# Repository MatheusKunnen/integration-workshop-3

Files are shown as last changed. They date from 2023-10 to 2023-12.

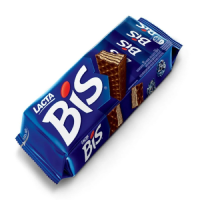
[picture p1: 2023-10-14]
server/images/bis.png

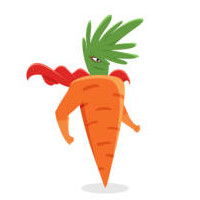
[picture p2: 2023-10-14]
server/images/p2i2.jpg

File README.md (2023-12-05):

# Snacks Control System

This project was created for the Integration Workshop 3 within the Computer Engineering curriculum during the second semester of 2023 at UTFPR University.

**Team Members**

- Alessandra Fernandes Lacerda
- Gabriel Henrique Linke
- Ivan Bauer Jr.
- Matheus Kunnen Ledesma _(Project Manager)_
- Meika Farias de Oliveira
- Patricia Abe Turato

**Orientators**

- Prof. Dr. Heitor Silvério Lopes
- Prof. Dr. João Alberto Fabro

## Overview

A frequent concern of parents is the difficulty in controlling their children's eating habits at school, as children need healthy snacks to support their growth and development. Unfortunately, many of the snacks provided in the school canteen are high in fat, sugar and salt. Furthermore, it is difficult to guarantee that children diagnosed with food allergies or intolerance do not eat foods containing ingredients that may cause a reaction. On top of that, kids might not know how to manage their money well and end up spending too much.

The project tries to solve these problems with a system that allows parents to manage the options of snacks shown to their kids, and a vending machine to distribute these snacks.

The mobile application allows parents to register their children in the system, select the specific snacks that will be available for them to buy and specify their daily budget. The vending machine identifies the child and shows all available authorized food options along with the available budget. Finally, when the desired product is selected, the machine asks for confirmation and then delivers the snack.

## Acknowledgements

The team would like to express their deepest gratitude to Professor Dr. Heitor Silvério Lopes and Professor Dr. João Alberto Fabro for their guidance and support during the development of the project. Also, the team is thankful to all the professors of Computer Engineering at UTFPR for their contributions to the team members academic growth. Their collective efforts in imparting knowledge and sharing experiences were fundamental to the development of capabilities that made this a successful project.

## Useful links

- Blog: https://alelacerda.notion.site/Snacks-Control-System-76155e9a51a641b1811bb6345904a688?pvs=4
- Video: https://youtu.be/sgXLWZ9KaMk

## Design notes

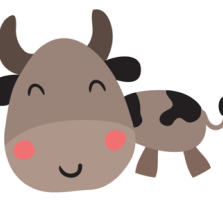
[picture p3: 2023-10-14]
server/images/p1i4.png

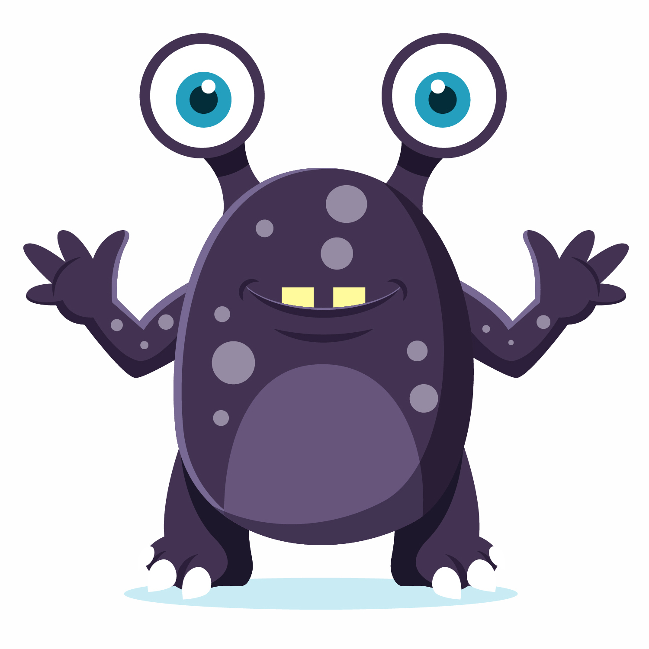
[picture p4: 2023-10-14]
server/images/p3i1.jpg

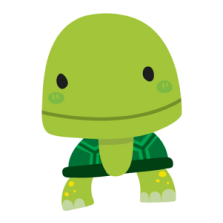
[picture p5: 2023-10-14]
server/images/p1i6.png

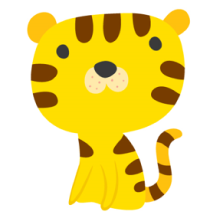
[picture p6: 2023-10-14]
server/images/p1i2.png

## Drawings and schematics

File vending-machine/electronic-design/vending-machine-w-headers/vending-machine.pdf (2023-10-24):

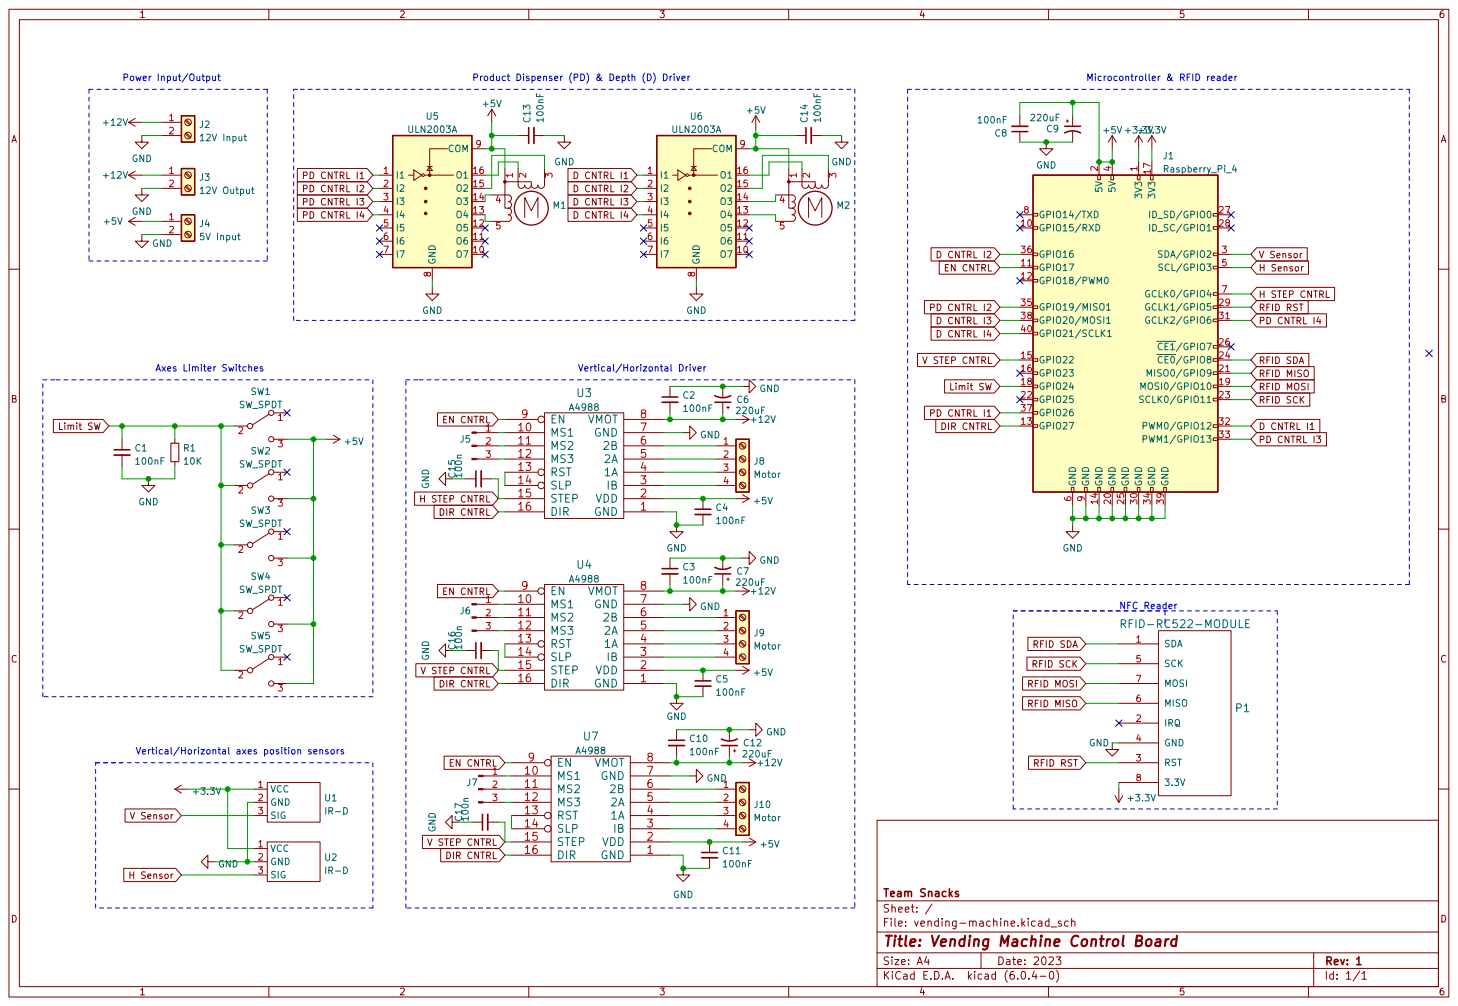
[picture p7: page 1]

8 COM 9 U6 ULN2003A GND GND GND

V Sensor H Sensor RFID RST PD CNTRL I4 PD CNTRL I3 H STEP CNTRL RFID SDA RFID MOSI RFID MISO

D CNTRL I1 RFID SCK RFID MOSI

EN CNTRL Limit SW

File: vending-machine.kicad_sch Sheet: / Team Snacks

Id: 1/1 Title: Vending Machine Control Board

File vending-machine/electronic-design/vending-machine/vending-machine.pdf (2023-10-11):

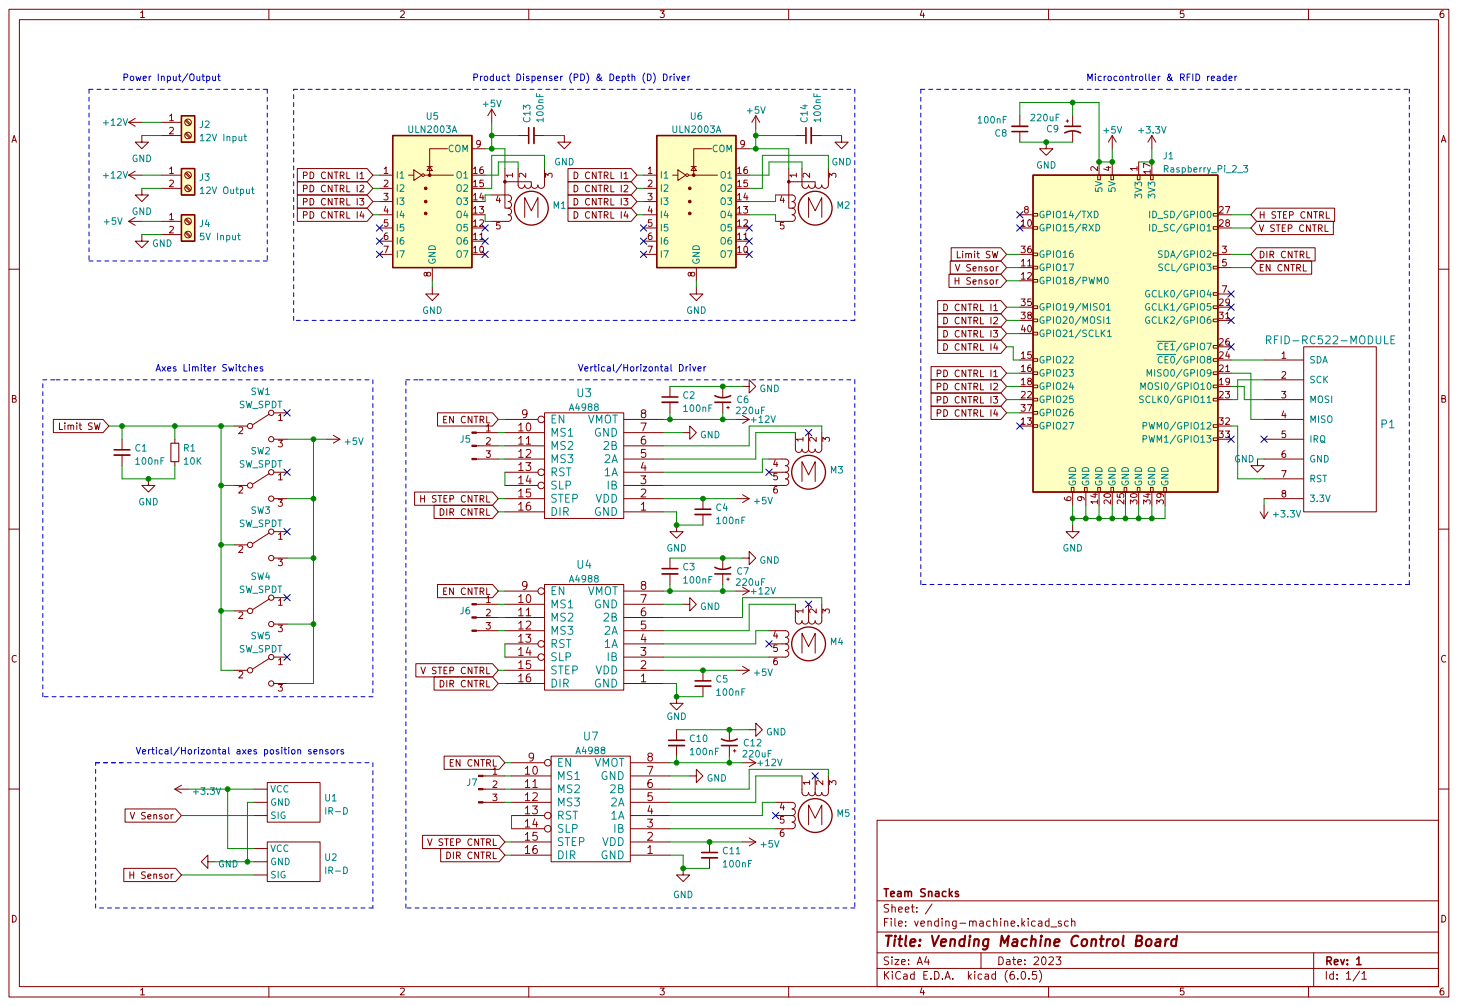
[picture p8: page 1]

H STEP CNTRL V STEP CNTRL EN CNTRL EN CNTRL

File: vending-machine.kicad_sch Sheet: / Team Snacks

Id: 1/1 Title: Vending Machine Control Board

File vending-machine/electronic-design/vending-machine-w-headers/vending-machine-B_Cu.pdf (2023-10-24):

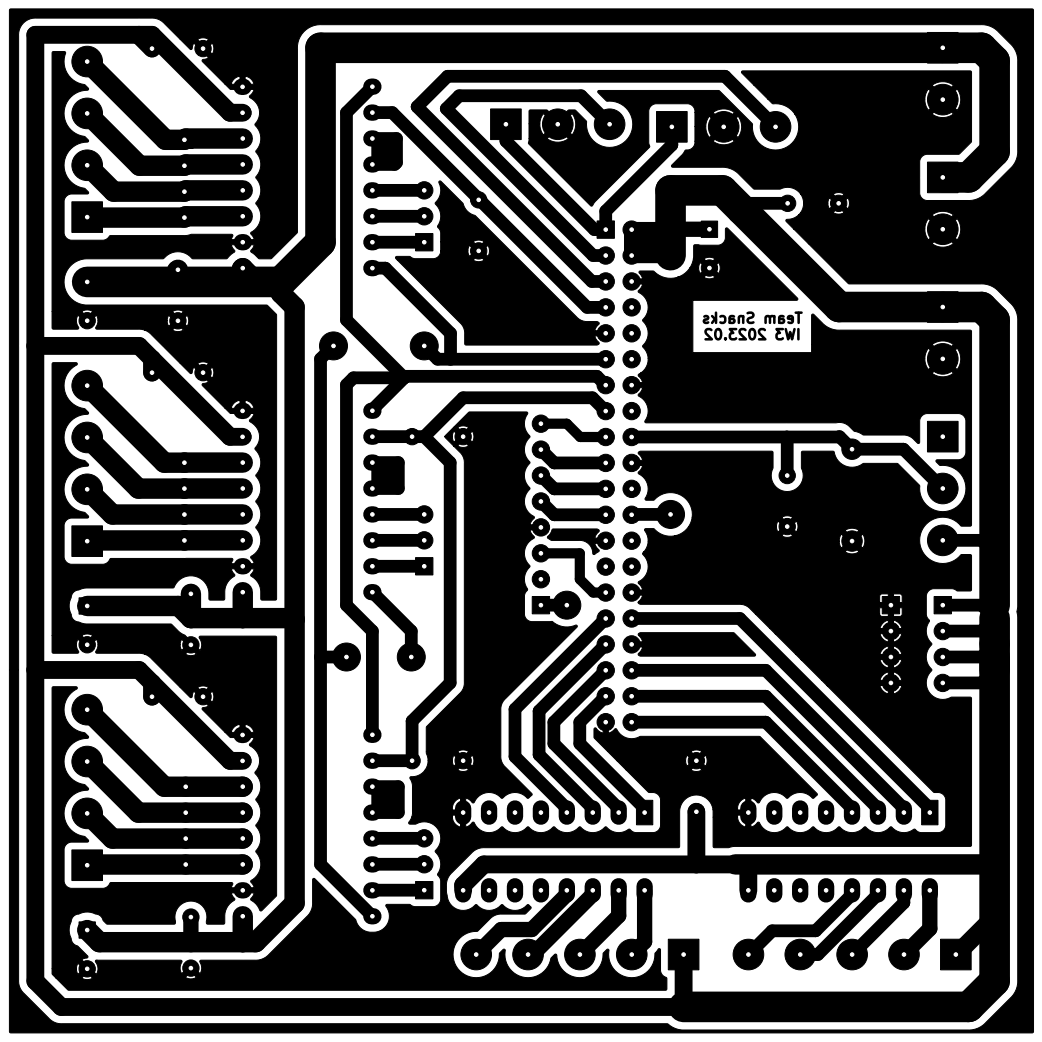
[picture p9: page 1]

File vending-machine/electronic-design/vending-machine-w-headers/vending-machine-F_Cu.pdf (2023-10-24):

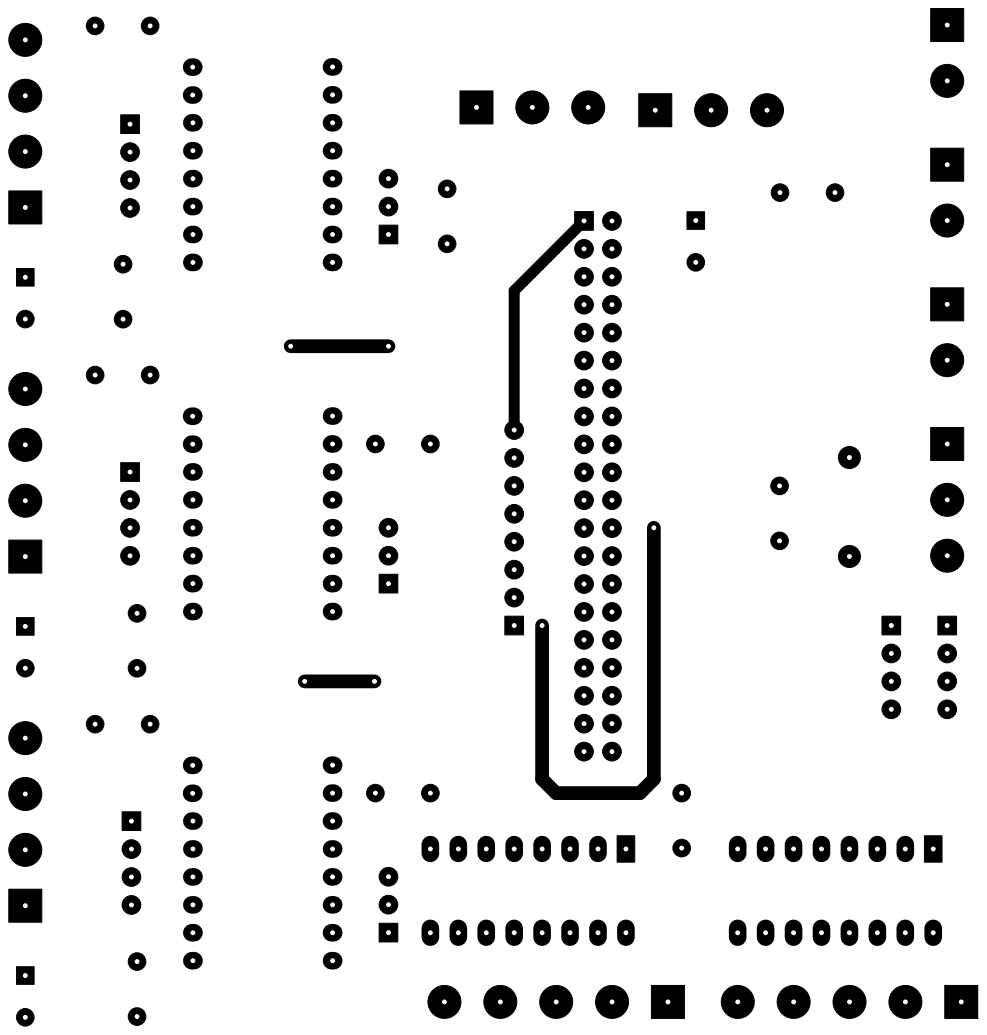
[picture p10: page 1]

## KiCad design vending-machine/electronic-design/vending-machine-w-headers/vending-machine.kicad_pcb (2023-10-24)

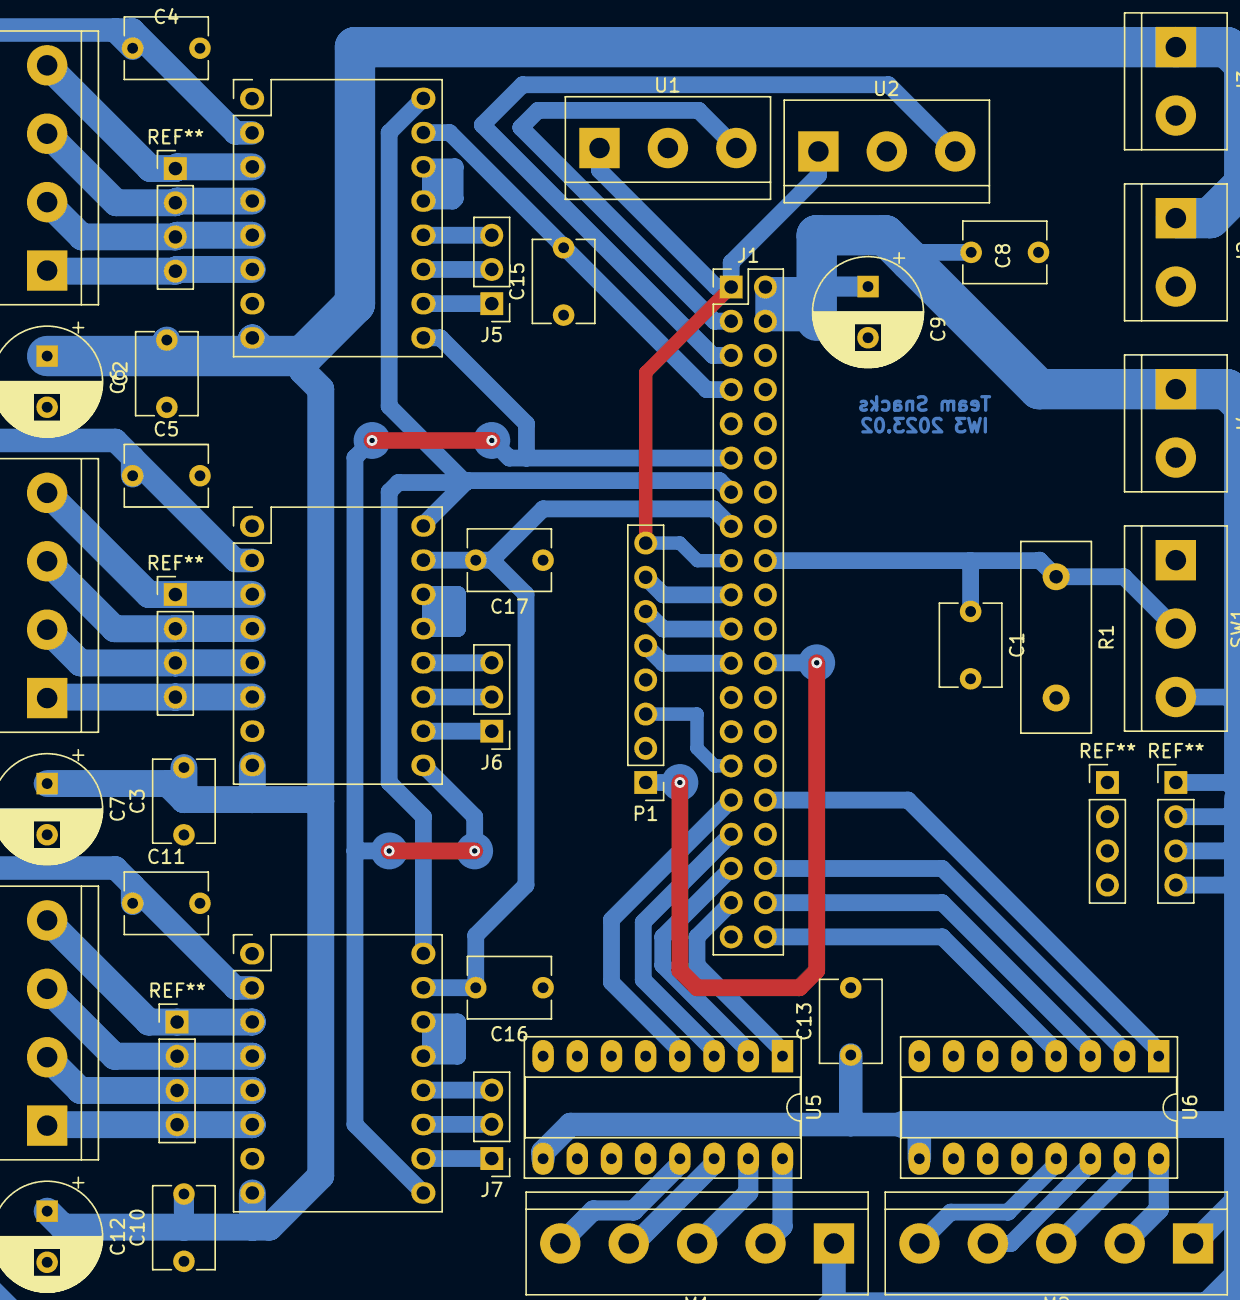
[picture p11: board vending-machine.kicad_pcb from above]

Board: 2 copper layers, 38 parts (0 on the bottom side), 56 nets.

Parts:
C1, C2, C3, C4, C5, C8, C10, C11, C13: 100nF; C_Disc_D6.0mm_W4.4mm_P5.00mm
C6, C7, C9, C12: 220uF; CP_Radial_D8.0mm_P3.80mm
C15, C16, C17: 100n; C_Disc_D6.0mm_W4.4mm_P5.00mm
J1: Raspberry_Pi_4; PinHeader_2x20_P2.54mm_Vertical
J2: 12V Input; TerminalBlock_bornier-2_P5.08mm
J3: 12V Output; TerminalBlock_bornier-2_P5.08mm
J4: 5V Input; TerminalBlock_bornier-2_P5.08mm
J5, J6, J7: Conn_01x03_Male; PinHeader_1x03_P2.54mm_Vertical
J8, J9, J10: Motor; TerminalBlock_bornier-4_P5.08mm
M1, M2: Stepper_Motor_unipolar_5pin; TerminalBlock_bornier-5_P5.08mm
P1: RFID-RC522-MODULE; PinHeader_1x08_P2.54mm_Vertical
R1: 10K; R_Box_L14.0mm_W5.0mm_P9.00mm
SW1: SW_SPDT; TerminalBlock_bornier-3_P5.08mm
U1, U2: IR-D; TerminalBlock_bornier-3_P5.08mm
U3, U4, U7: A4988; Pololu_A4988
U5, U6: ULN2003A; DIP-16_W7.62mm_Socket_LongPads

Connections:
+3V3: J1.1 (3V3), J1.17 (3V3), P1.8 (3.3V), U1.1 (VCC), U2.1 (VCC)
+5V: C4.1, C5.1, C8.2, C9.1, C11.1, C13.1, J1.2 (5V), J1.4 (5V), J4.1, M1.1, M2.1, SW1.3 (C), U3.2 (VDD), U4.2 (VDD), U5.9 (COM), U6.9 (COM), U7.2 (VDD)
+12V: C2.2, C3.2, C6.1, C7.1, C10.2, C12.1, J2.1, J3.1, U3.8 (VMOT), U4.8 (VMOT), U7.8 (VMOT)
D CNTRL I1: J1.32 (PWM0/GPIO12), U6.1 (I1)
D CNTRL I2: J1.36 (GPIO16), U6.2 (I2)
D CNTRL I3: J1.38 (GPIO20/MOSI1), U6.3 (I3)
D CNTRL I4: J1.40 (GPIO21/SCLK1), U6.4 (I4)
DIR CNTRL: J1.13 (GPIO27), U3.16 (DIR), U4.16 (DIR), U7.16 (DIR)
EN CNTRL: J1.11 (GPIO17), U3.9 (EN), U4.9 (EN), U7.9 (EN)
GND: C1.2, C2.1, C3.1, C4.2, C5.2, C6.2, C7.2, C8.1, C9.2, C10.1, C11.2, C12.2, C13.2, C15.1, C16.1, C17.1, J1.6 (GND), J1.9 (GND), J1.14 (GND), J1.20 (GND), J1.25 (GND), J1.30 (GND), J1.34 (GND), J1.39 (GND), J2.2, J3.2, J4.2, P1.4 (GND), R1.2, U1.2 (GND), U2.2 (GND), U3.1 (GND), U3.7 (GND), U4.1 (GND), U4.7 (GND), U5.8 (GND), U6.8 (GND), U7.1 (GND), U7.7 (GND)
H STEP CNTRL: C15.2, J1.7 (GCLK0/GPIO4), U3.15 (STEP)
H Sensor: J1.5 (SCL/GPIO3), U2.3 (SIG)
Limit SW: C1.1, J1.18 (GPIO24), R1.1, SW1.2 (B)
unnamed: J5.1, U3.10 (MS1)
unnamed: J5.2, U3.11 (MS2)
unnamed: J5.3, U3.12 (MS3)
unnamed: J6.1, U4.10 (MS1)
unnamed: J6.2, U4.11 (MS2)
unnamed: J6.3, U4.12 (MS3)
unnamed: J7.1, U7.10 (MS1)
unnamed: J7.2, U7.11 (MS2)
unnamed: J7.3, U7.12 (MS3)
unnamed: J8.1, U3.6 (2B)
unnamed: J8.2, U3.5 (2A)
unnamed: J8.3, U3.4 (1A)
unnamed: J8.4, U3.3 (IB)
unnamed: J9.1, U4.6 (2B)
unnamed: J9.2, U4.5 (2A)
unnamed: J9.3, U4.4 (1A)
unnamed: J9.4, U4.3 (IB)
unnamed: J10.1, U7.6 (2B)
unnamed: J10.2, U7.5 (2A)
unnamed: J10.3, U7.4 (1A)
unnamed: J10.4, U7.3 (IB)
unnamed: M1.2, U5.16 (O1)
unnamed: M1.3 (-), U5.15 (O2)
unnamed: M1.4, U5.14 (O3)
unnamed: M1.5, U5.13 (O4)
unnamed: M2.2, U6.16 (O1)
unnamed: M2.3 (-), U6.15 (O2)
unnamed: M2.4, U6.14 (O3)
unnamed: M2.5, U6.13 (O4)
unnamed: U3.13 (RST), U3.14 (SLP)
unnamed: U4.13 (RST), U4.14 (SLP)
unnamed: U7.13 (RST), U7.14 (SLP)
PD CNTRL I1: J1.37 (GPIO26), U5.1 (I1)
PD CNTRL I2: J1.35 (GPIO19/MISO1), U5.2 (I2)
PD CNTRL I3: J1.33 (PWM1/GPIO13), U5.3 (I3)
PD CNTRL I4: J1.31 (GCLK2/GPIO6), U5.4 (I4)
RFID MISO: J1.21 (MISO0/GPIO9), P1.6 (MISO)
RFID MOSI: J1.19 (MOSI0/GPIO10), P1.7 (MOSI)
RFID RST: J1.29 (GCLK1/GPIO5), P1.3 (RST)
RFID SCK: J1.23 (SCLK0/GPIO11), P1.5 (SCK)
RFID SDA: J1.24 (~CE0/GPIO8), P1.1 (SDA)
V STEP CNTRL: C16.2, C17.2, J1.15 (GPIO22), U4.15 (STEP), U7.15 (STEP)
V Sensor: J1.3 (SDA/GPIO2), U1.3 (SIG)

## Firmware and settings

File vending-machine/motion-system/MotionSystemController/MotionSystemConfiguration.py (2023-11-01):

from dataclasses import dataclass

@dataclass
class MotionSystemConfiguration:

    en_pin:int = 17
    dir_pin:int = 27

    step_pin_h:int = 22
    step_pin_v:int = 4

    pd_motor_pins:(int) = (26, 19, 13, 6)
    depth_motor_pins:(int) = (12, 16, 20, 21)

    limiter_pin:int = 24
    sensor_pin_h:int = 3
    sensor_pin_v:int = 2

    def input_pins(self):
        return [self.limiter_pin, self.sensor_pin_h, self.sensor_pin_v]
    
    def output_pins(self):
        pins = [self.en_pin, self.dir_pin, self.step_pin_h, self.step_pin_v]
        
        for pin in self.pd_motor_pins:
            pins.append(pin)
        for pin in self.depth_motor_pins:
            pins.append(pin)

        return pins
    
    def default_high_pins(self):
        return [self.en_pin]
    
    def default_low_pins(self):
        pins = [self.dir_pin, self.step_pin_h, self.step_pin_v]

        for pin in self.pd_motor_pins:
            pins.append(pin)
        for pin in self.depth_motor_pins:
            pins.append(pin)

        return pins

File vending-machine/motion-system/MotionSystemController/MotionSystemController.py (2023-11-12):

from .MotionSystemConfiguration import MotionSystemConfiguration
from .Axis import Axis
from .A4988Driver import A4988Driver
from .ULN2003Driver import ULN2003Driver
from .StepperDriver import *
from .LimiterSwitch import LimiterSwitch
from .ReflectanceSensor import ReflectanceSensor
from .ProductDispenser import ProductDispenser
from .MotionSystemMonitor import MotionSystemMonitor

from multiprocessing import Process, Queue
import json

try:
    import RPi.GPIO as GPIO
except:
    import Mock.GPIO as GPIO
    
class MotionSystemController:

    __DEFAULT_PRODUCTS = [
        {"id": 1, "v_pos": 450, "h_pos": 450, "depth":4096*7, "turns":4096+1024},
        {"id": 2, "v_pos": 450, "h_pos": 2825, "depth":4096*7, "turns":4096+1024},
        {"id": 3, "v_pos": 450, "h_pos": 5225, "depth":4096*7, "turns":4096+1024},
        {"id": 4, "v_pos": 4850, "h_pos": 450, "depth":4096*7, "turns":4096+1024},
        {"id": 5, "v_pos": 4850, "h_pos": 2825, "depth":4096*7, "turns":4096+1024},
        {"id": 6, "v_pos": 4850, "h_pos": 5225, "depth":4096*5, "turns":4096+1024},
    ]

    def __init__(self, config: MotionSystemConfiguration):
        self.__products = MotionSystemController.__DEFAULT_PRODUCTS
        self.__config = config

        self.__initialize_gpio()

        self.__h_motor: StepperDriver = A4988Driver(config.step_pin_h, config.dir_pin)
        self.__v_motor: StepperDriver = A4988Driver(config.step_pin_v, config.dir_pin)

        self.__pd_motor: StepperDriver = ULN2003Driver(config.pd_motor_pins)
        self.__depth_motor: StepperDriver = ULN2003Driver(config.depth_motor_pins)

        self.__limiter_sw: LimiterSwitch = LimiterSwitch(config.limiter_pin)
        self.__h_sensor: ReflectanceSensor = ReflectanceSensor(config.sensor_pin_h, 'Horizontal')
        self.__v_sensor: ReflectanceSensor = ReflectanceSensor(config.sensor_pin_v, 'Vertical')

        self.__h_axis: Axis = Axis('Horizontal', self.__h_motor, self.__limiter_sw, self.__h_sensor)
        self.__v_axis: Axis = Axis('Vertical', self.__v_motor, self.__limiter_sw, self.__v_sensor)
        self.__product_dispenser = ProductDispenser(self.__pd_motor, self.__depth_motor, self.__limiter_sw)

        self.__monitor = MotionSystemMonitor(self.__limiter_sw, self.__config.en_pin)

        self.__req_queue = Queue()
        self.__res_queue = Queue()

        self.__process = Process(name="motion-system-controller", target=self.__process_entry, daemon=True)

        self.__monitor.start()
        self.__process.start()


    def provide_product(self, product_id:int):
        while not self.__res_queue.empty():
            self.__res_queue.get(timeout=0.01)
        print(f'Product {product_id} addded to queue')
        self.__req_queue.put(product_id)
        
        success, msg = self.__res_queue.get(block=True)
        print('Product', success, msg)
        if not success:
            raise Exception(msg)
        
        return success


    def __get_product_position(self, product_id: int):
        for product in self.__products:
            if product['id'] == product_id:
                return product["v_pos"], product["h_pos"], product["depth"], product["turns"]
        raise KeyError(f'Invalid product id {product_id}')
        

    def __initialize(self):
        try:
            self.__disable_axes()
            self.__product_dispenser.initialize()
            self.__enable_axes()
            self.__h_axis.initialize()
            self.__v_axis.initialize()
            # self.manual_mode_menu()
        finally:
            self.__disable_axes()

    def __load_products_pos(self):
        filename = f"./products_positions.json"
        try:
            data = None
            
            with open(filename, 'r') as file:
                data = json.load(file)
            
            if data is None:
                raise Exception('Invalid file')
            
            if 'products' in data:
                self.__products = data['products']
            else:
                print(f'Invalid products positions file for {self.__name}')
                self.__products = MotionSystemController.__DEFAULT_PRODUCTS
        except:
            self.__products = MotionSystemController.__DEFAULT_PRODUCTS

    def __process_entry(self):
        print('Motion System Controller thread started')

        print('Initializing motion system')
        self.__initialize()
        
        while True:
            try:
                product_id = self.__req_queue.get(block=True)

                self.__load_products_pos()
                v_pos, h_pos, depth, turns = self.__get_product_position(product_id)
                res_send = False
                print(f"Providing product {v_pos}, {h_pos}, {depth}, {turns}")
                try:
                    self.__enable_axes(True)

                    can_use_axes_queue = self.__can_use_axes_queue(v_pos, h_pos)

                    self.__v_axis.move_to_position(v_pos, queue=can_use_axes_queue)
                    self.__h_axis.move_to_position(h_pos, queue=can_use_axes_queue)

                    self.__v_axis.join()
                    self.__h_axis.join()

                    self.__disable_axes()
                    
                    self.__product_dispenser.provide_product(depth, turns)
                    
                    self.__res_queue.put((True, product_id))
                    res_send = True

                    self.__product_dispenser.home(depth)

                    if self.__req_queue.empty():
                        self.__enable_axes(True)
                        self.__h_axis.move_to_position(0, queue=True)
                        self.__v_axis.move_to_position(0, queue=True)
                        self.__v_axis.join()
                        self.__h_axis.join()
                        self.__enable_axes(False)
                        self.__v_axis.home()
                        self.__h_axis.home()
                except Exception as e:
                    if not res_send:
                        self.__res_queue.put((False, str(e)))
                finally:
                    self.__disable_axes()
            except Exception as e:
                print(e)
                if not res_send:
                    self.__res_queue.put((False, str(e)))

    def __can_use_axes_queue(self, v_pos:int, h_pos:int):
        v_steps = v_pos - self.__v_axis.position() 
        h_steps = h_pos - self.__h_axis.position() 
        return v_steps == 0 or h_steps == 0 or (v_steps > 0 and h_steps > 0) or (v_steps < 0 and h_steps < 0)
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

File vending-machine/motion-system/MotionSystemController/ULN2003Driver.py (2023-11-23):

from .StepperDriver import *
from time import sleep

try:
    import RPi.GPIO as GPIO
except:
    import Mock.GPIO as GPIO

class ULN2003Driver(StepperDriver):

    __STEP_SEQ = [(1,0,0,1),
                    (1,0,0,0),
                    (1,1,0,0),
                    (0,1,0,0),
                    (0,1,1,0),
                    (0,0,1,0),
                    (0,0,1,1),
                    (0,0,0,1)
                    ]
    
    def __init__(self, pins):
        StepperDriver.__init__(self)
        self.__pins = tuple(pins)
        self.__current_step = 0
        GPIO.output(self.__pins, (0,0,0,0))
        self.start_process()

    def step(self, steps:int, velocity=None, queue:bool=False):
        if steps == 0:
            return
        
        if queue:
            self.add_step_to_queue(steps, velocity)
            return 
        
        dir = StepperDirection.CW if steps > 0 else StepperDirection.CCW

        if velocity is None:
            velocity = self._velocity

        delay = self.__get_delay(velocity)

        steps = abs(steps)
        for _ in range(steps):
            GPIO.output(self.__pins, ULN2003Driver.__STEP_SEQ[self.__current_step])
            sleep(delay)
            self.__next_step(dir)

        self.__current_step = 0
        GPIO.output(self.__pins, (0,0,0,0))

    def __get_delay(self, velocity: StepperVelocity):
        if velocity == StepperVelocity.NORMAL:
            return 0.000600
        elif velocity == StepperVelocity.FAST:
            return 0.000500
        else:
            return 0.000900
        
    def __next_step(self, direction: StepperDirection):
        if direction==StepperDirection.CW:
            self.__current_step = (self.__current_step - 1) % len(ULN2003Driver.__STEP_SEQ)
        else:
            self.__current_step = (self.__current_step + 1) % len(ULN2003Driver.__STEP_SEQ)

    def __del__(self):
        GPIO.output(self.__pins, (0,0,0,0))

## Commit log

2023-10-03 Main board schematic
    [vending-machine.kicad_pcb, vending-machine.kicad_sch]
2023-10-05 Schematic design
    [vending-machine-w-headers.kicad_sch, vending-machine.kicad_pcb, vending-machine.kicad_sch]
2023-10-08 Vending machine PDB final design
    [vending-machine.kicad_pcb, vending-machine.kicad_sch]
2023-10-11 Create custom button component
2023-10-12 Alter global styles and button component
2023-10-24 Stepper drivers
2023-10-24 Sensors & switches reading
2023-10-27 Add socket server to the motion system
2023-10-28 Add limiter switch implementation
2023-10-29 Add stepper drivers
2023-10-29 Adds budget and snacks to register child flow
2023-10-30 Improve axis calibration procedure
    Add move_to_pos method
2023-10-30 Bug fix in stepper drivers
    [A4988Driver.py, ULN2009Driver.py]
2023-10-31 Update velocities for ULN2009Driver
2023-10-31 Add logic to improve coupling
2023-10-31 Add slots default mapping
2023-11-06 Reflectance sensor implemented
2023-11-11 Update default slots positions
2023-11-11 Disable motors after steps ULN2003Driver
2023-11-11 Fix typo in ULN2009Driver
    [MotionSystemController.py, ULN2003Driver.py]
2023-11-11 Add Process to stepper drivers
2023-11-11 Avoid home if there's another request
    [A4988Driver.py, MotionSystemController.py, ProductDispenser.py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]
